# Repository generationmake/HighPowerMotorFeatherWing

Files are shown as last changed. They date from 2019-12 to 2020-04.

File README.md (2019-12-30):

# HighPowerMotorFeatherWing
HighPowerMotorFeatherWing with Infineon IFX007T drivers for two DC motors, up to 40V and 55A, compatible to Adafruit Feather

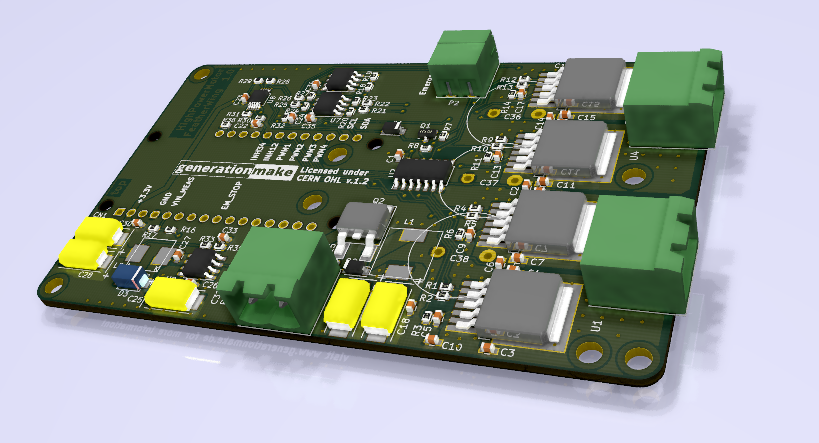
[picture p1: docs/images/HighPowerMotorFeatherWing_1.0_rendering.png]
HighPowerMotorFeatherWing rendering


## PCB

### Top

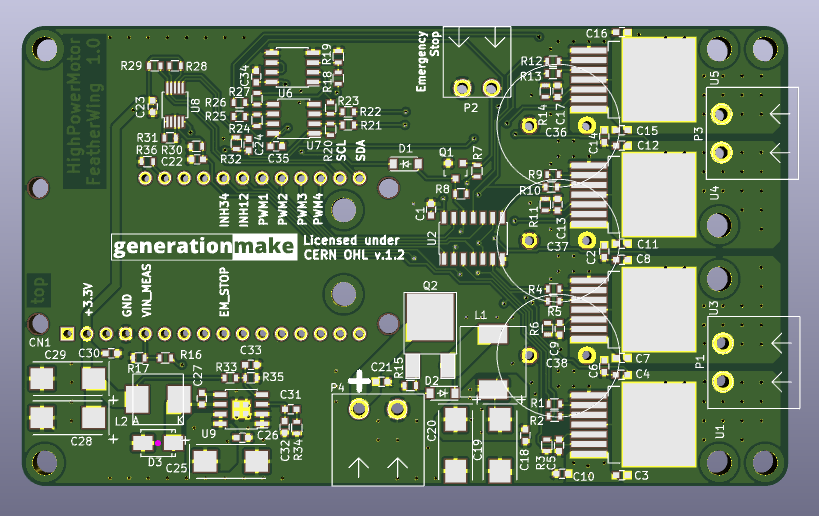
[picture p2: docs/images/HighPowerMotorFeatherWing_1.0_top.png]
HighPowerMotorFeatherWing PCB top


### Bottom

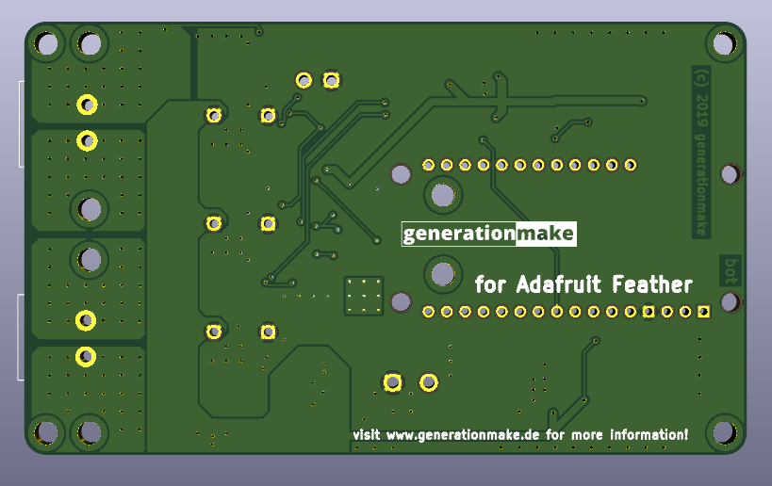
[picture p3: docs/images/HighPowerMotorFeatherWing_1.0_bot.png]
HighPowerMotorFeatherWing PCB bot


## License

This hardware is licensed under the CERN OHL v. 1.2

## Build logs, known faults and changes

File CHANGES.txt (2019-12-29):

HighPowerMotorFeatherWing - Motor driver feather wing for Adafruit Feather
see full project documentation at https://github.com/generationmake/HighPowerMotorFeatherWing

changes

version 1.0 - 2019-12-29
* initial release

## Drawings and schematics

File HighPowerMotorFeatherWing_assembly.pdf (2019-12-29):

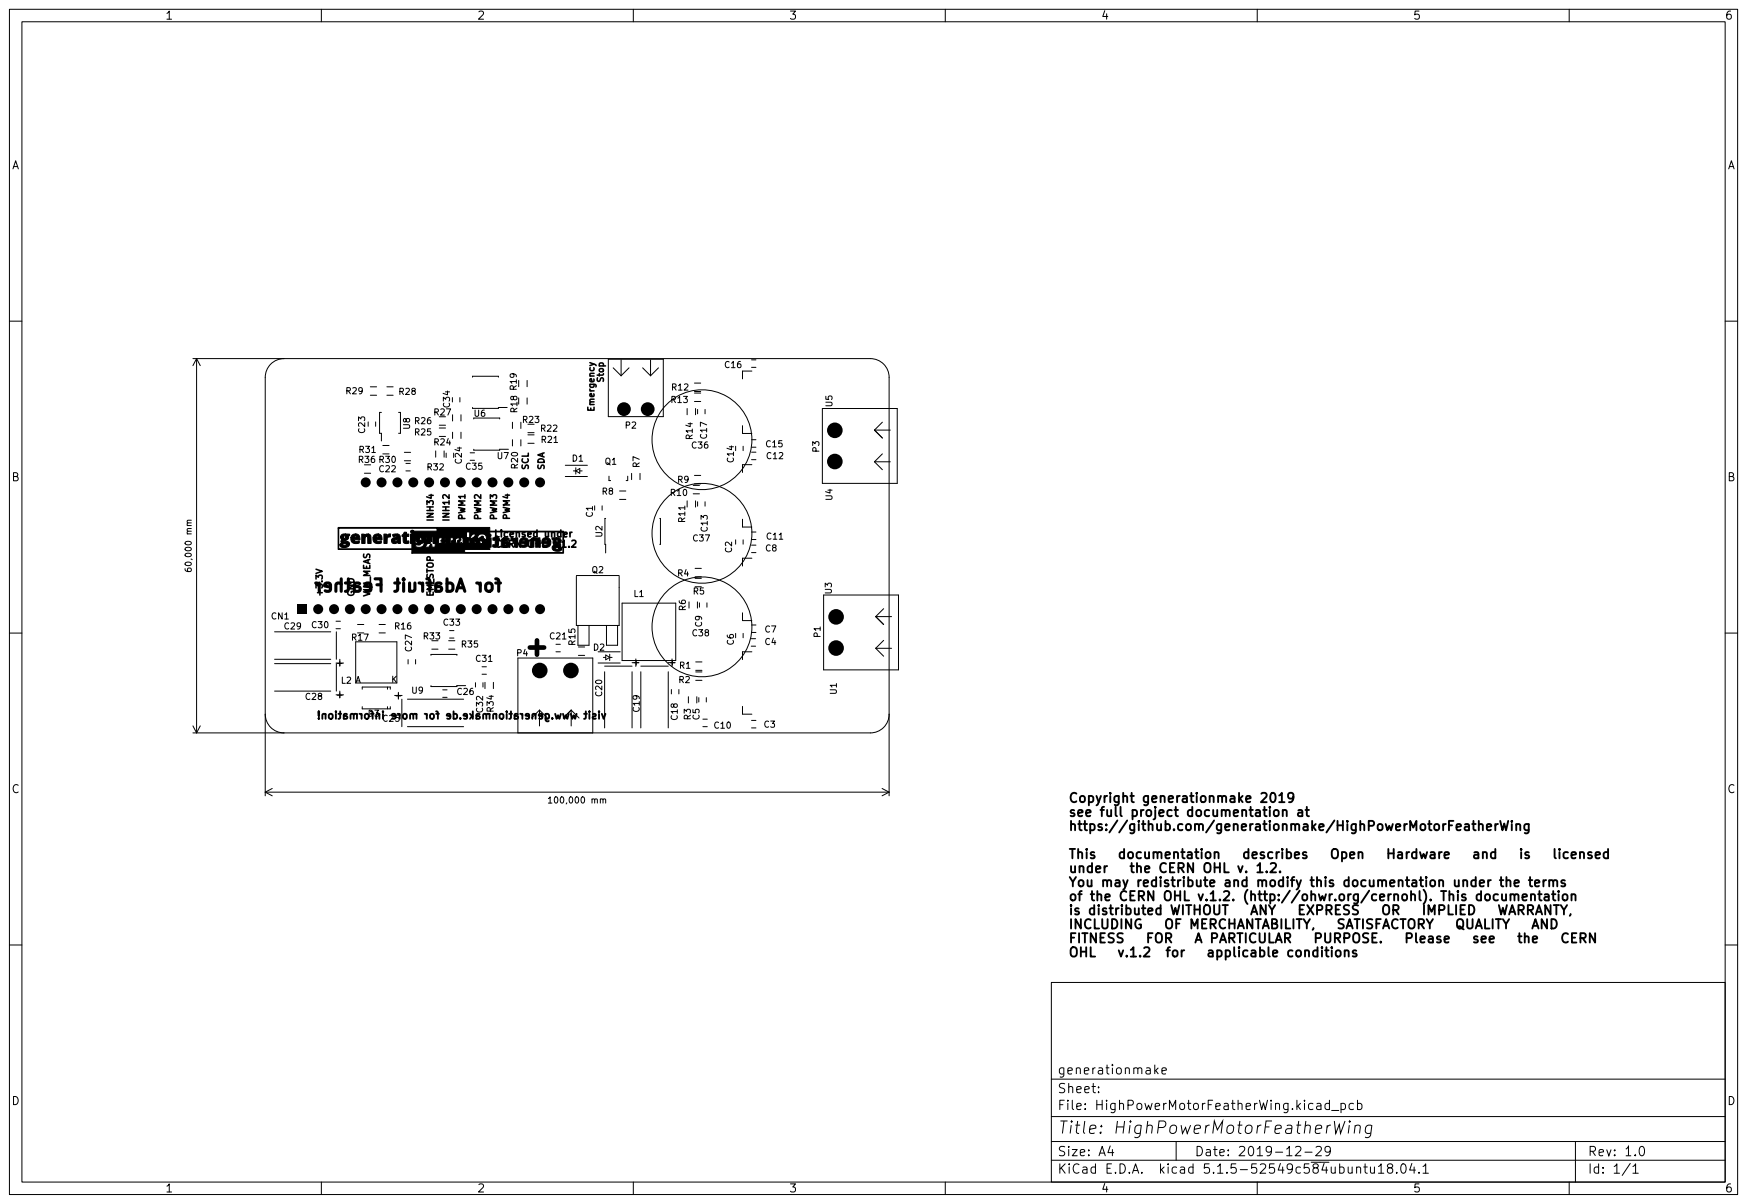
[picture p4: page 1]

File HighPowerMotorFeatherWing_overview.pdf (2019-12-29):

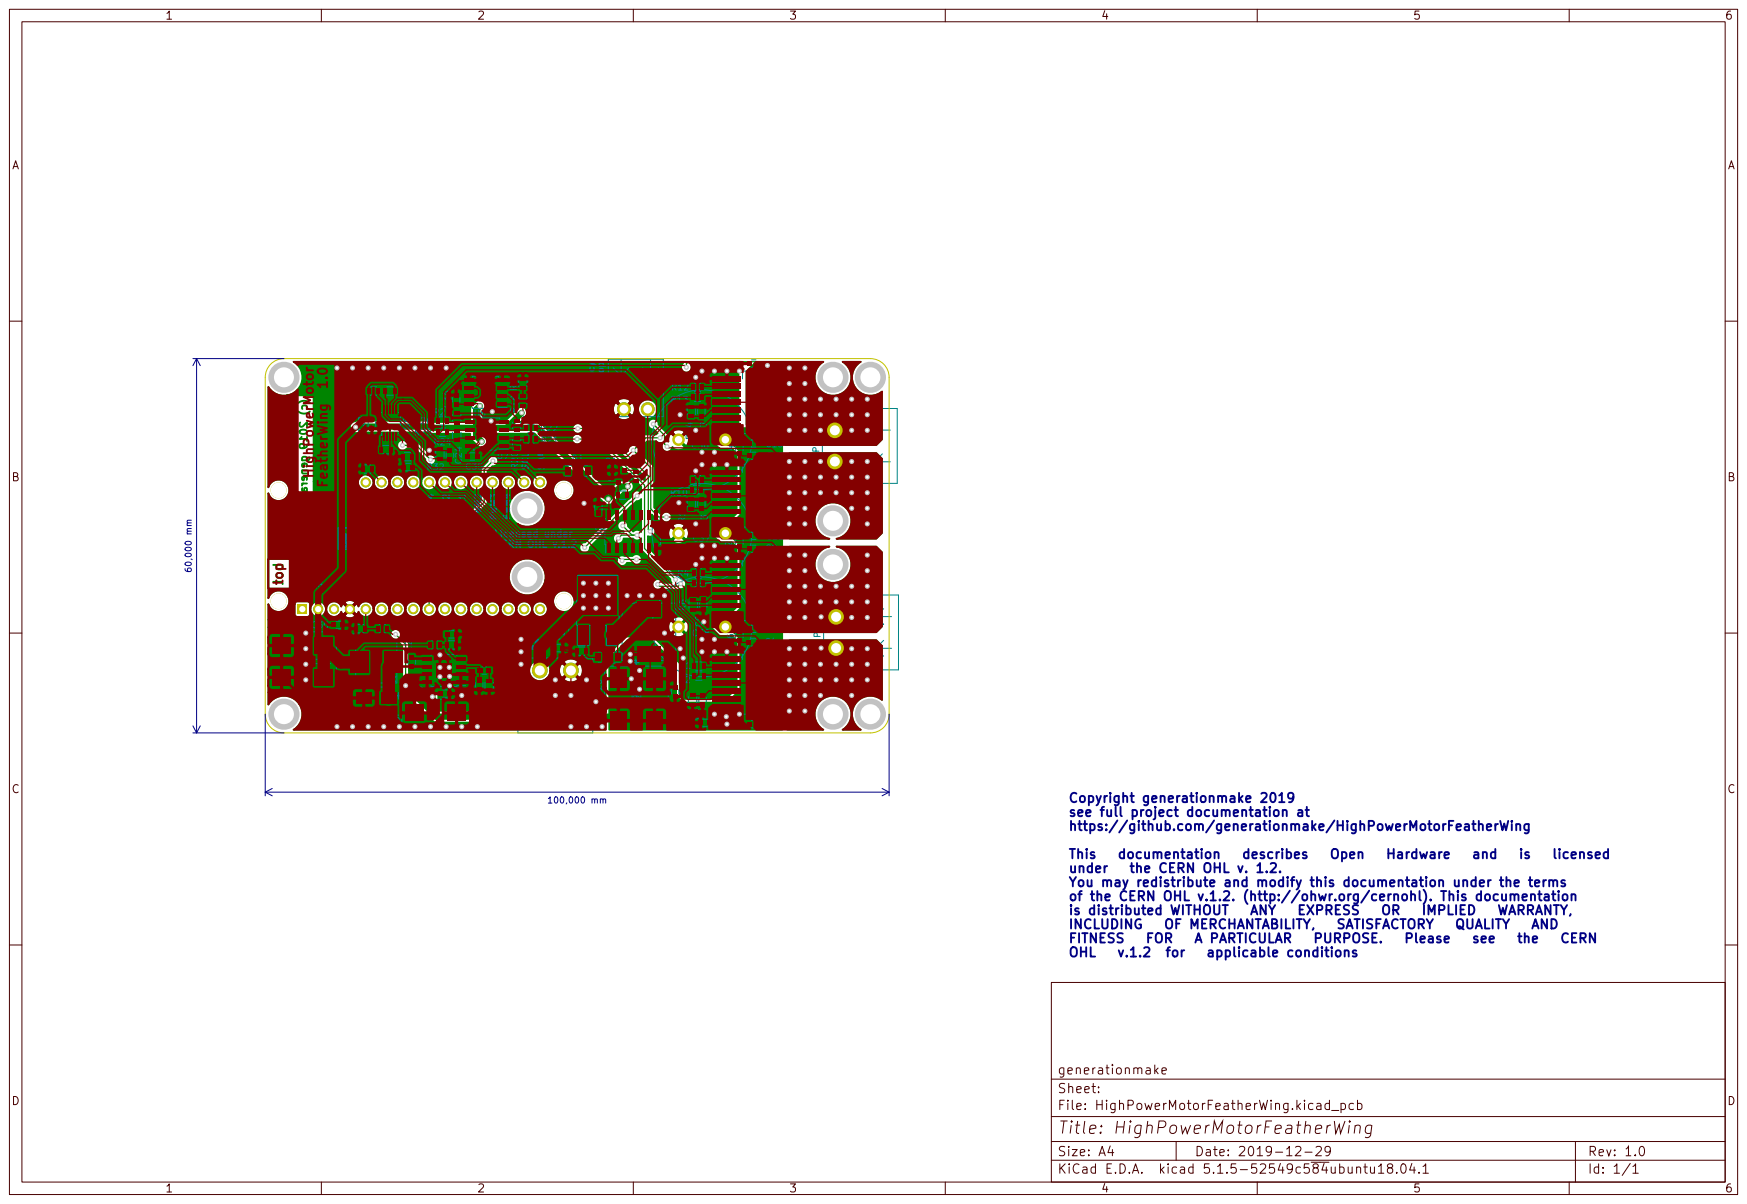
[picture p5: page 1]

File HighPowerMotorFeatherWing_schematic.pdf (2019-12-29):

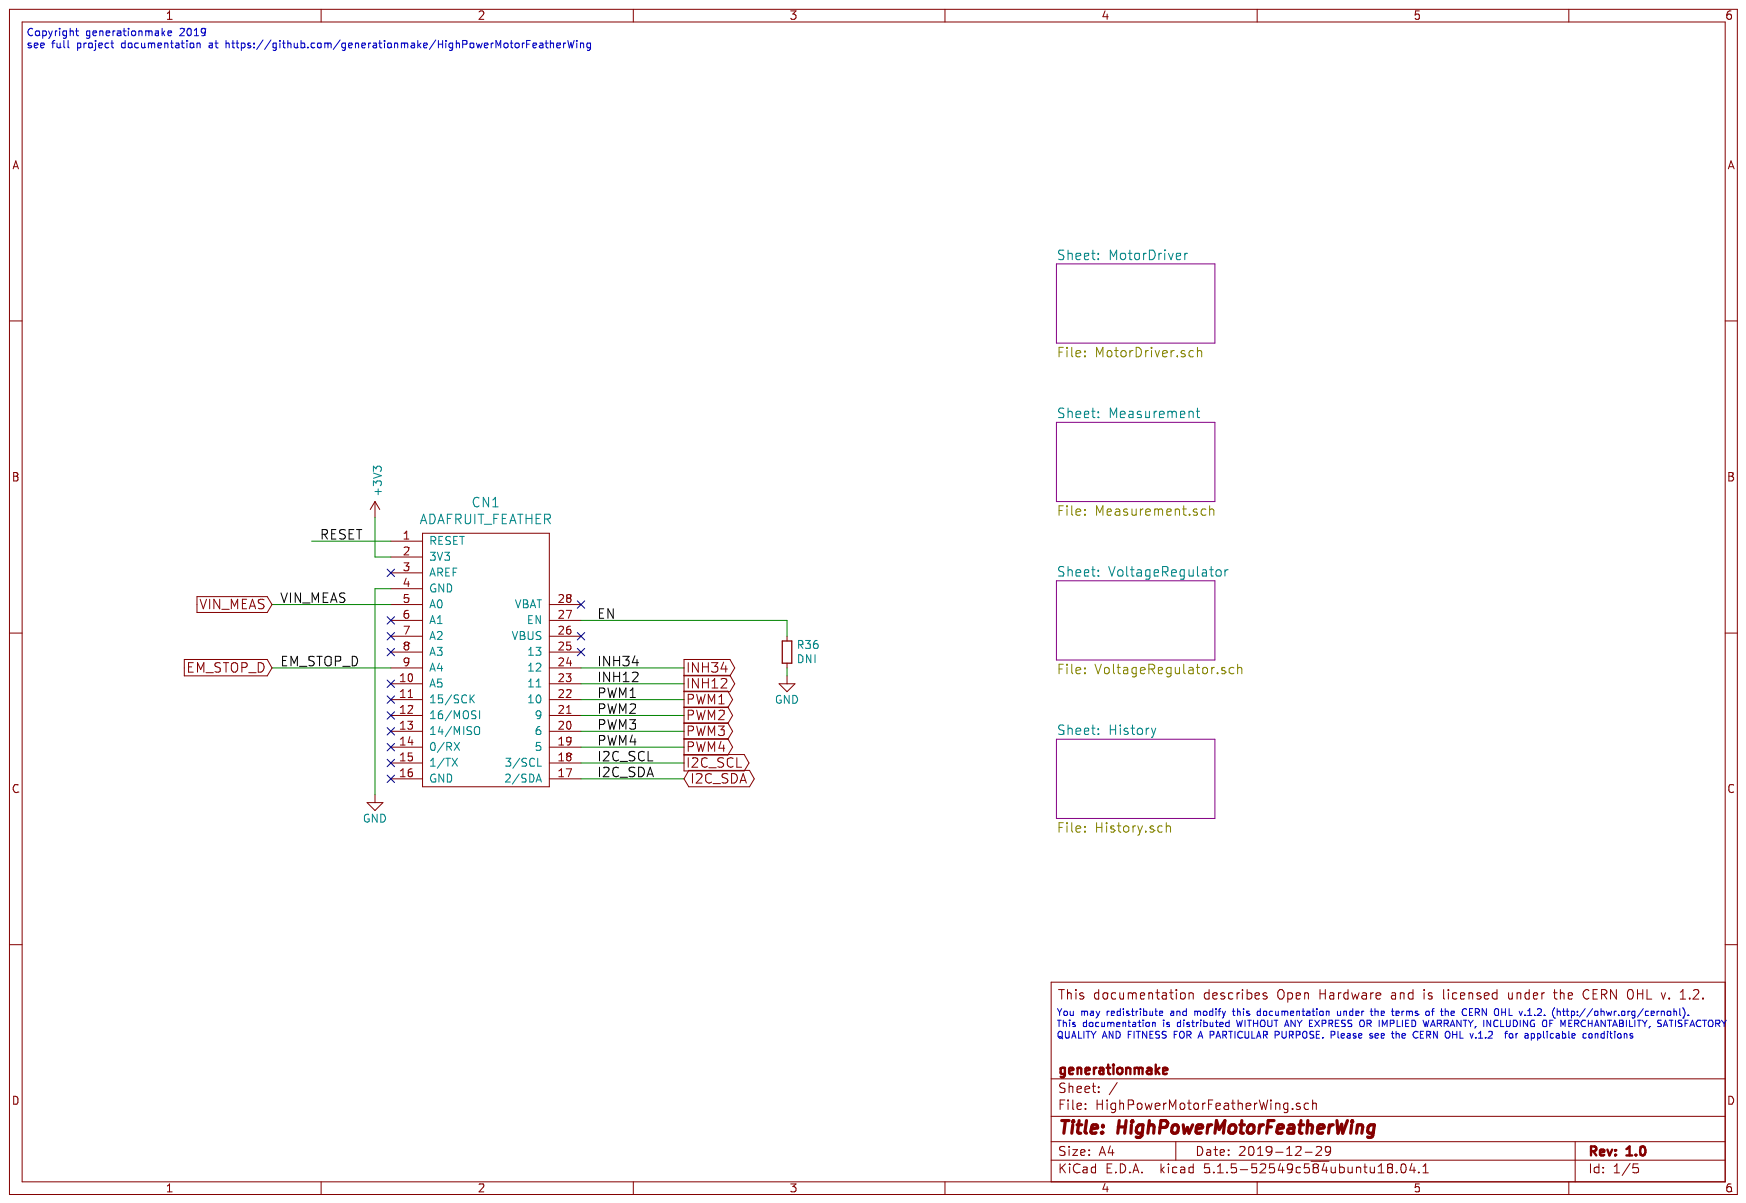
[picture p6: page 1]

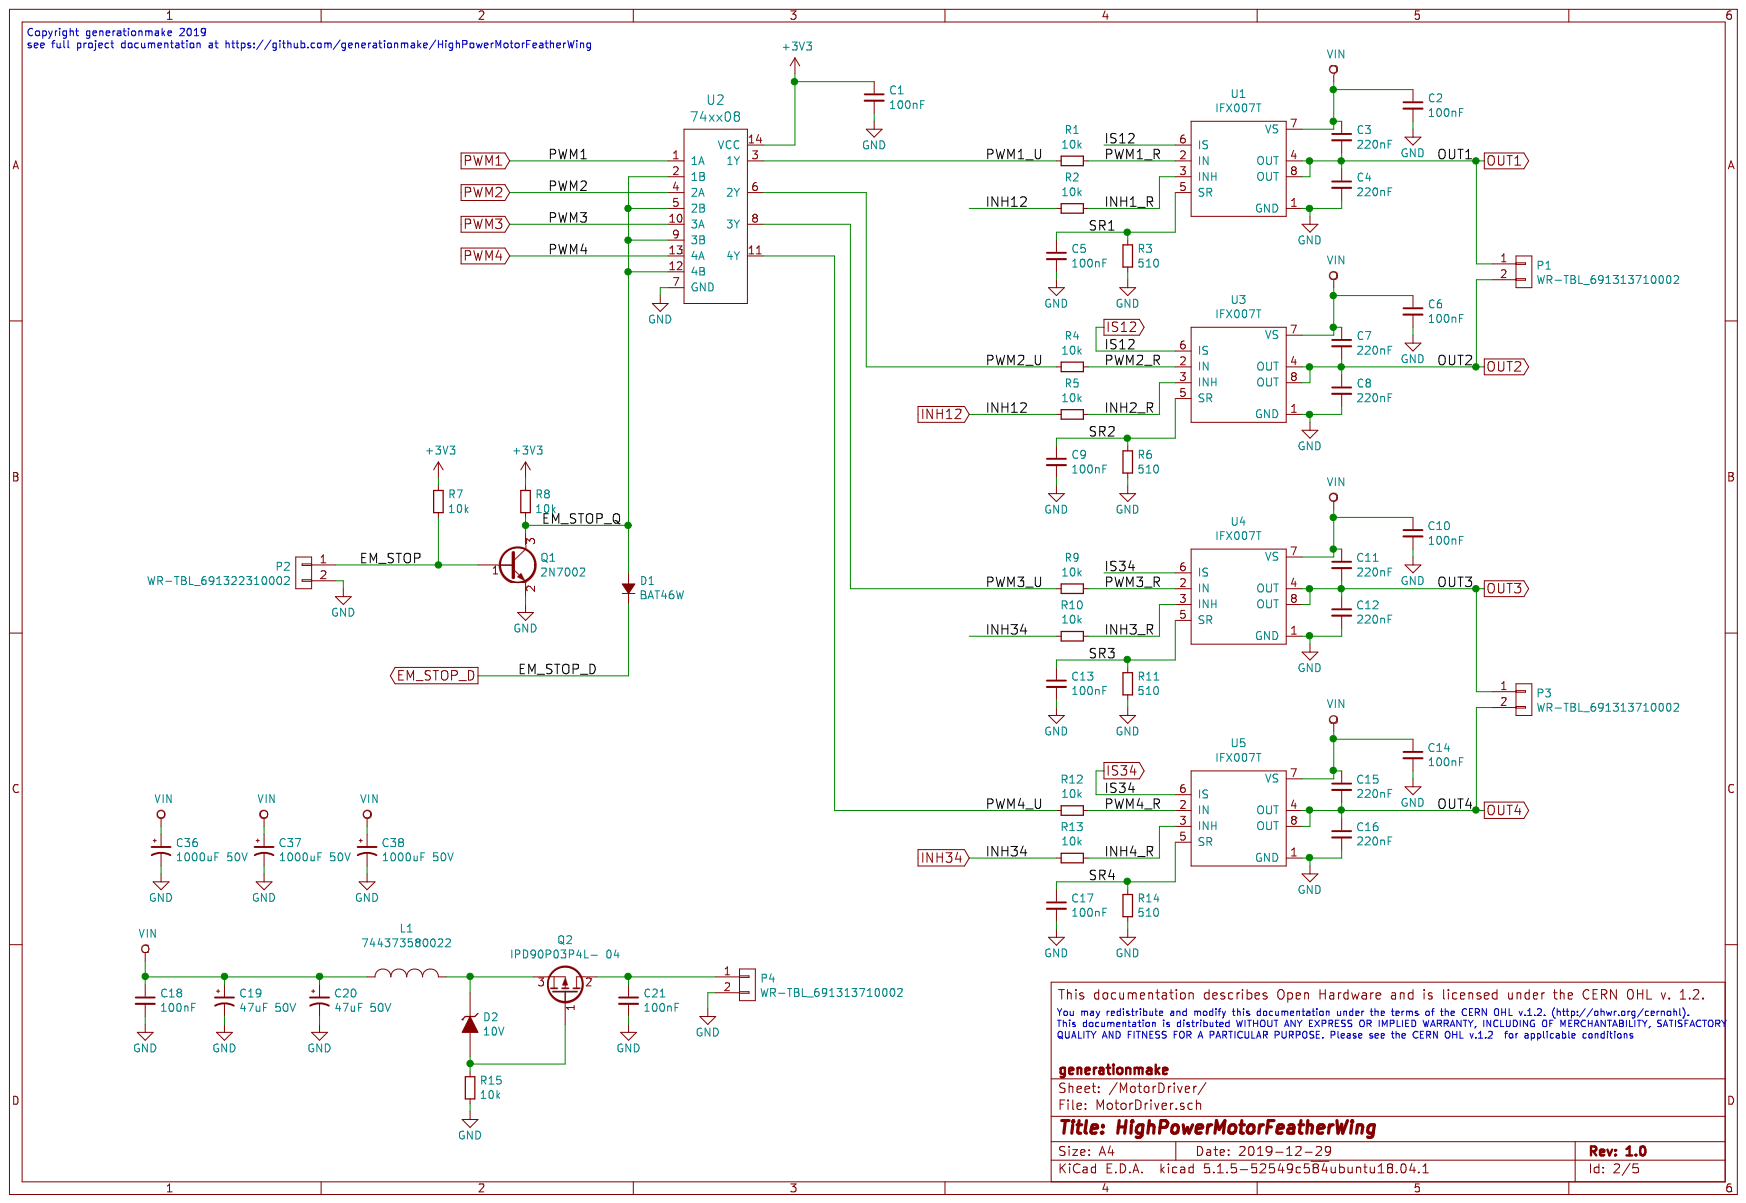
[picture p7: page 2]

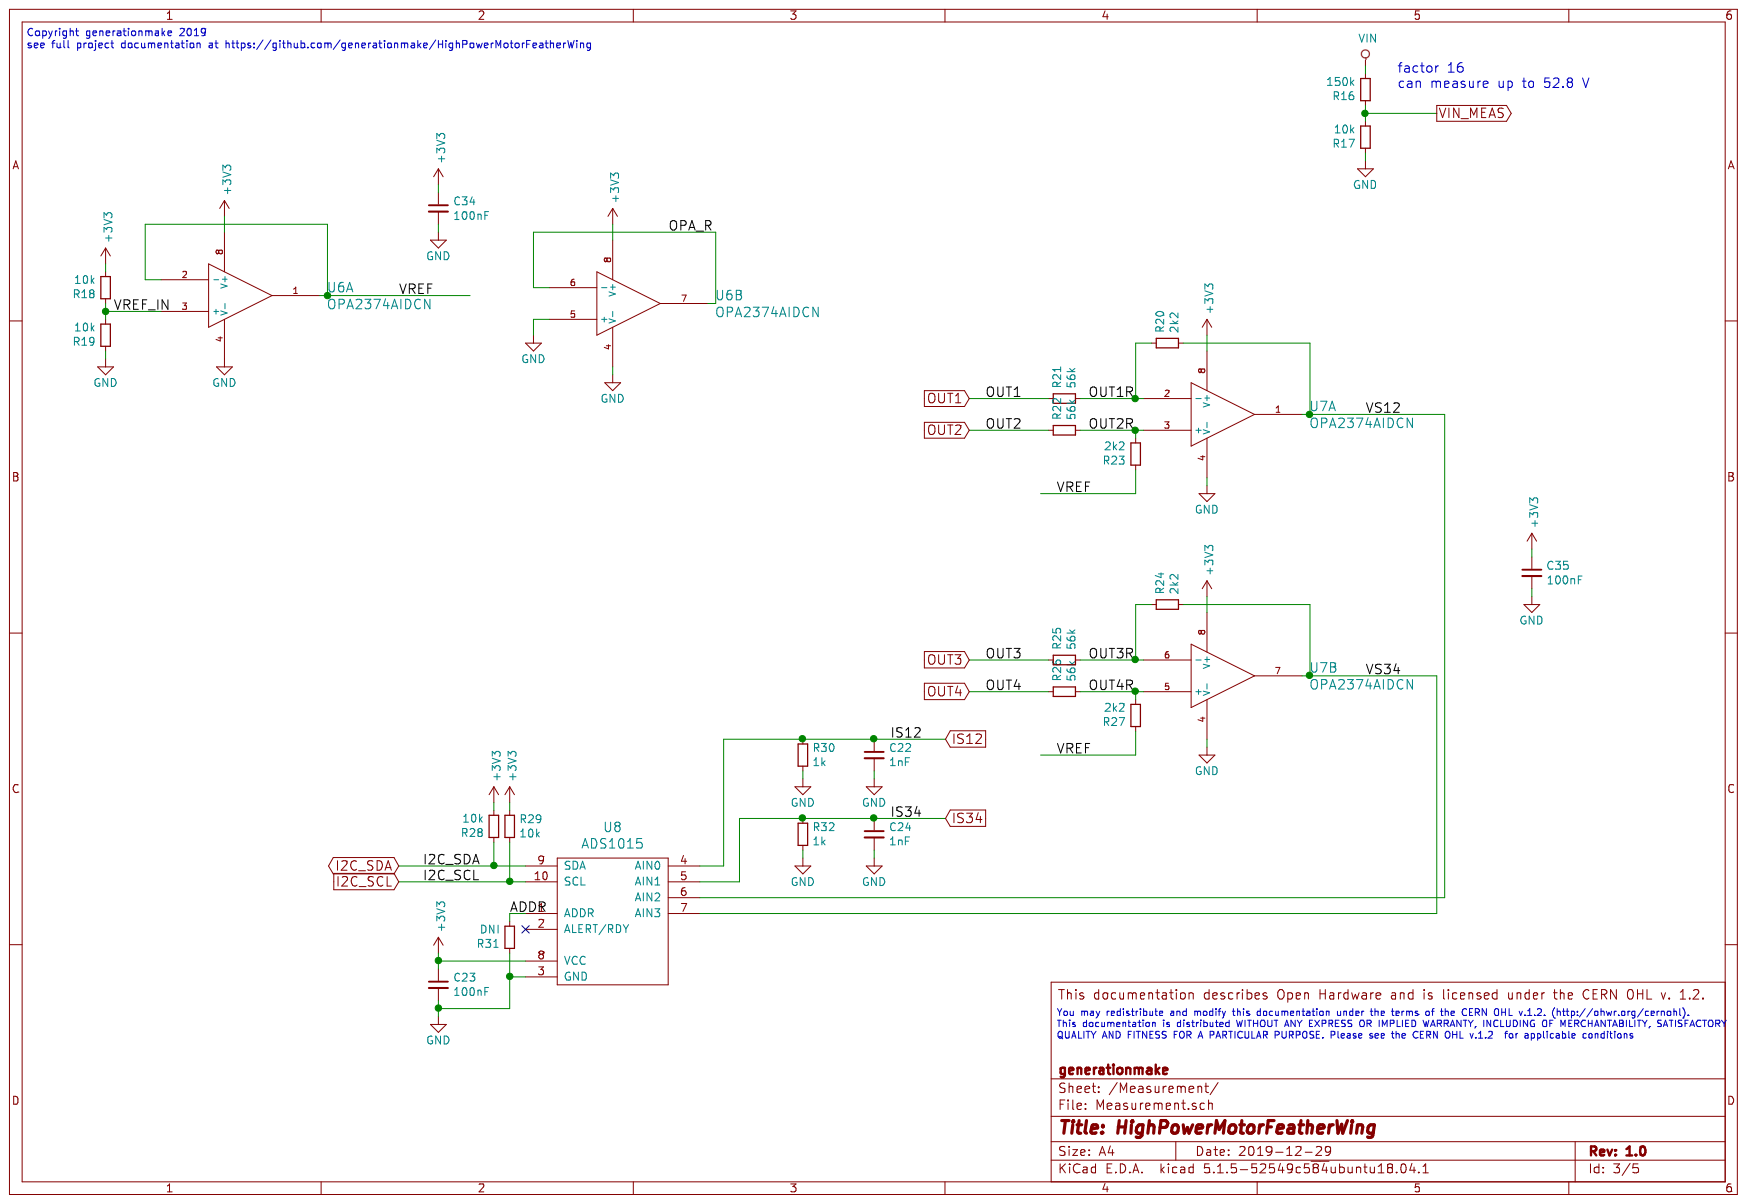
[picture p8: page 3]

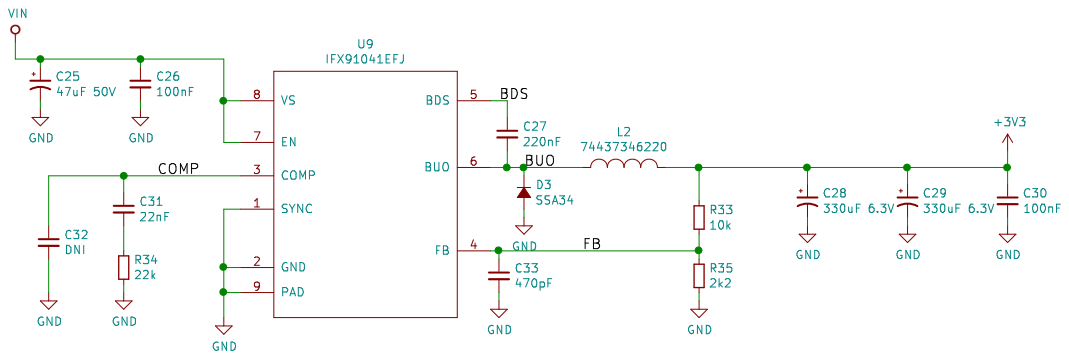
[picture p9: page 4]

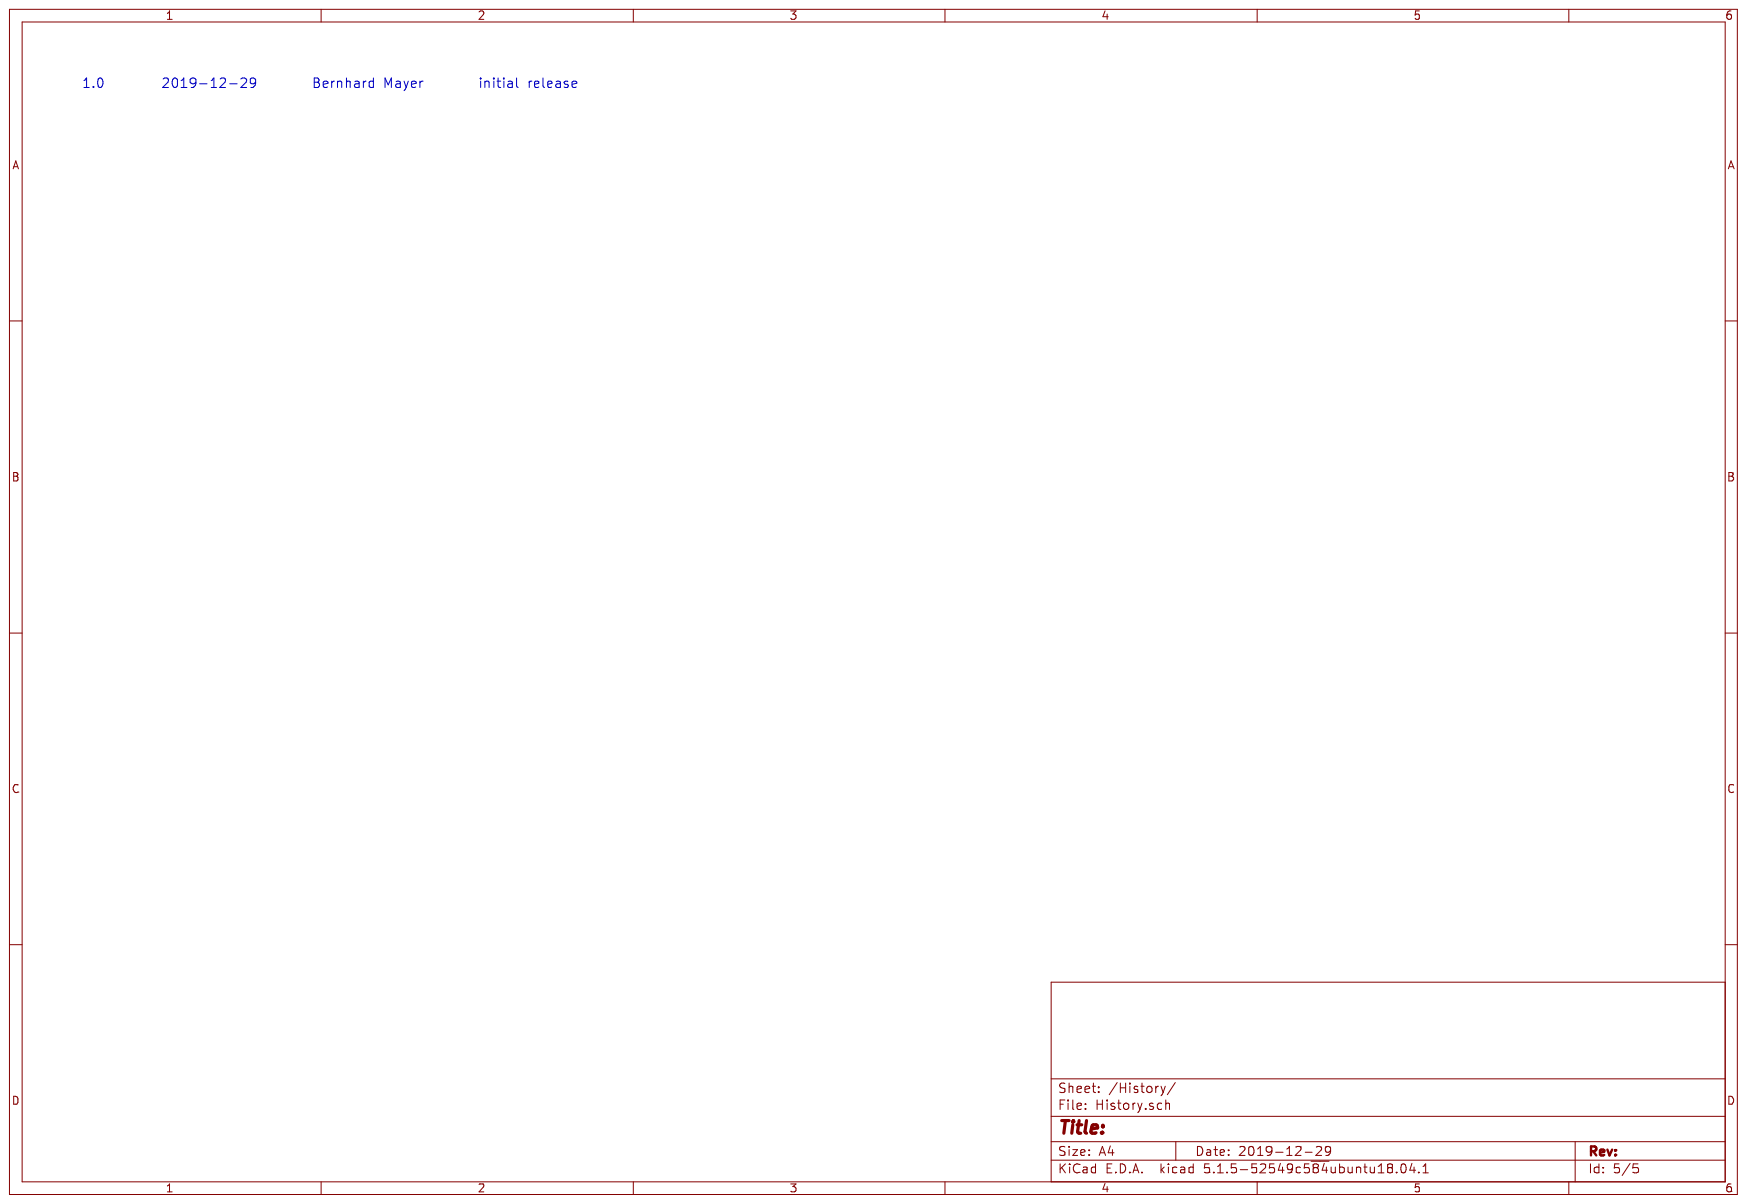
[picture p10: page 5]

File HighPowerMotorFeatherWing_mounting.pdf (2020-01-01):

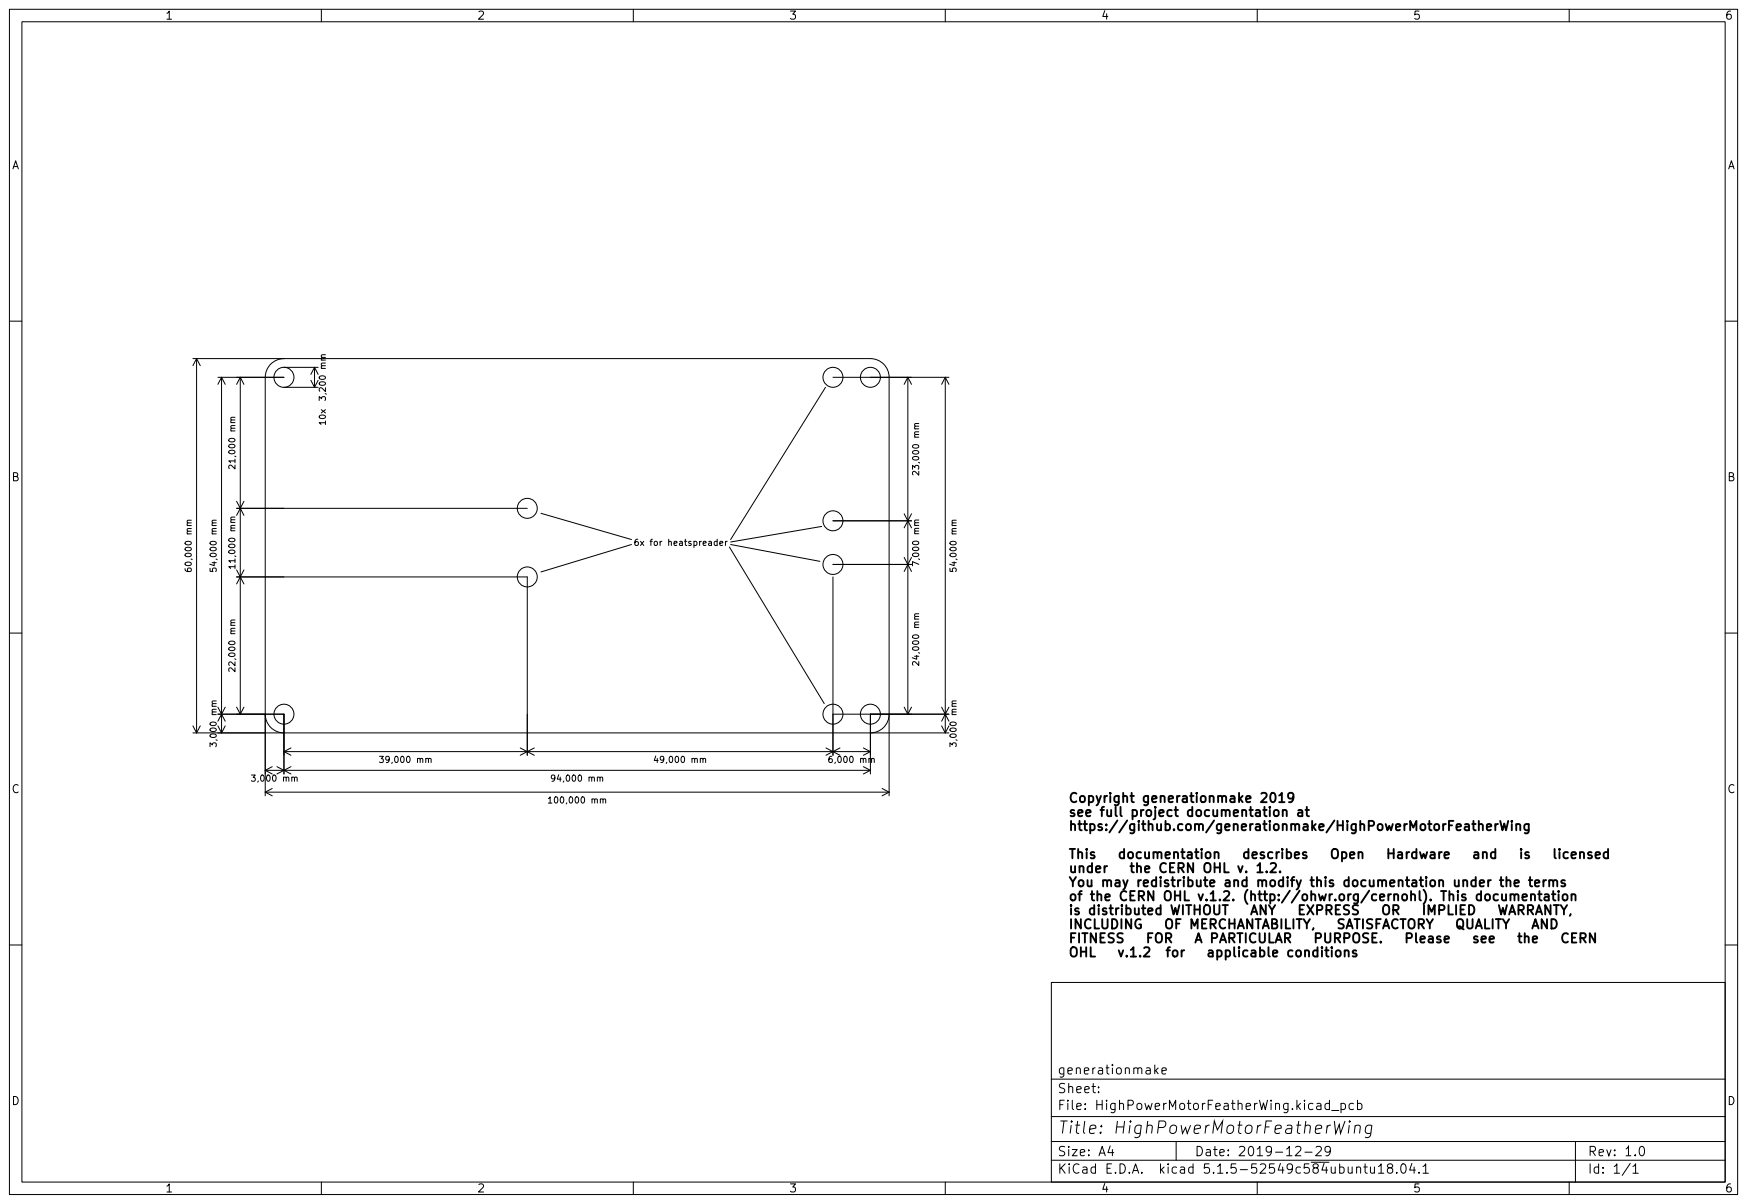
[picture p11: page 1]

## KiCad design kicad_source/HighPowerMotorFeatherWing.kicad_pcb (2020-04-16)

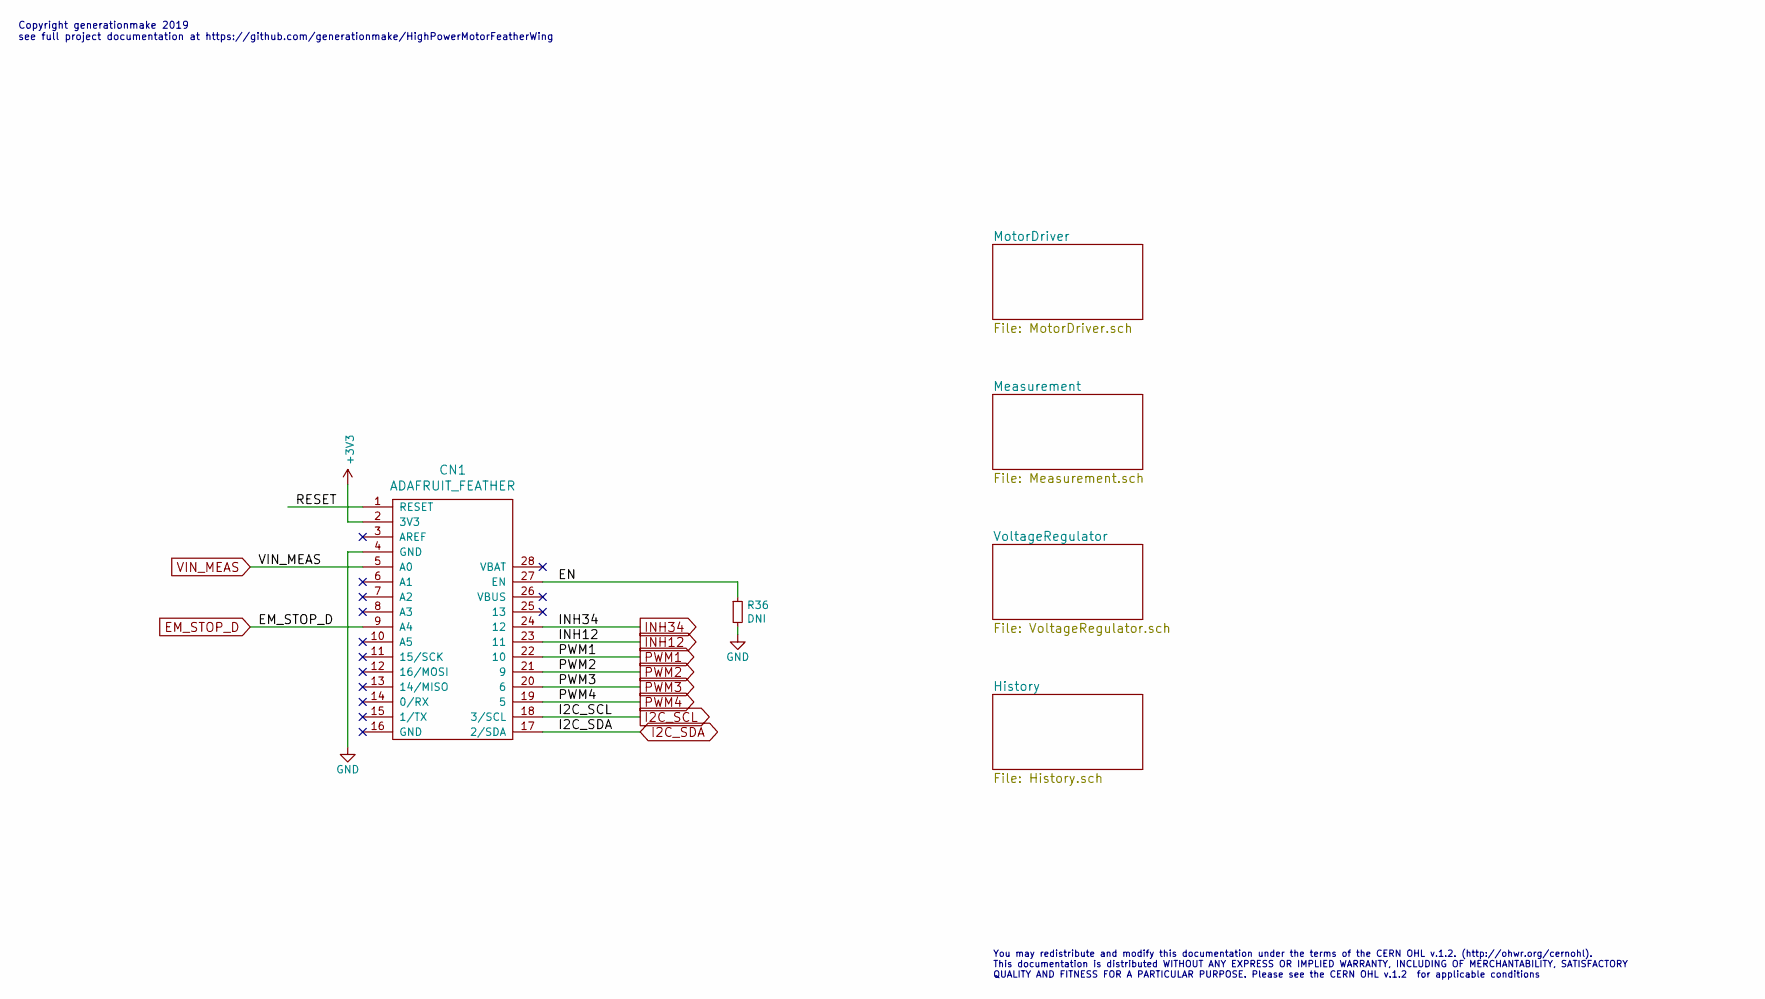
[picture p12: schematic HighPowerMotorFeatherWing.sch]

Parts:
CN1: ADAFRUIT_FEATHER; ADAFRUIT_FEATHER_HOLES
R36: DNI; R_0603

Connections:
+3V3: CN1.2 (3V3); also elsewhere on the board
/EN: CN1.27 (EN), R36.1
EM_STOP_D: CN1.9 (A4); also elsewhere on the board
GND: CN1.4 (GND), R36.2; also elsewhere on the board
I2C_SCL: CN1.18 (3/SCL); also elsewhere on the board
I2C_SDA: CN1.17 (2/SDA); also elsewhere on the board
INH12: CN1.23 (11); also elsewhere on the board
INH34: CN1.24 (12); also elsewhere on the board
PWM1: CN1.22 (10); also elsewhere on the board
PWM2: CN1.21 (9); also elsewhere on the board
PWM3: CN1.20 (6); also elsewhere on the board
PWM4: CN1.19 (5); also elsewhere on the board
VIN_MEAS: CN1.5 (A0); also elsewhere on the board

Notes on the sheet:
Copyright generationmake 2019 see full project documentation at https://github.com/generationmake/HighPowerMotorFeatherWing
You may redistribute and modify this documentation under the terms of the CERN OHL v.1.2. (http://ohwr.org/cernohl). This documentation is distributed WITHOUT ANY EXPRESS OR IMPLIED WARRANTY, INCLUDING OF MERCHANTABILITY, SATISFACTORY QUALITY AND FITNESS FOR A PARTICULAR PURPOSE. Please see the CER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

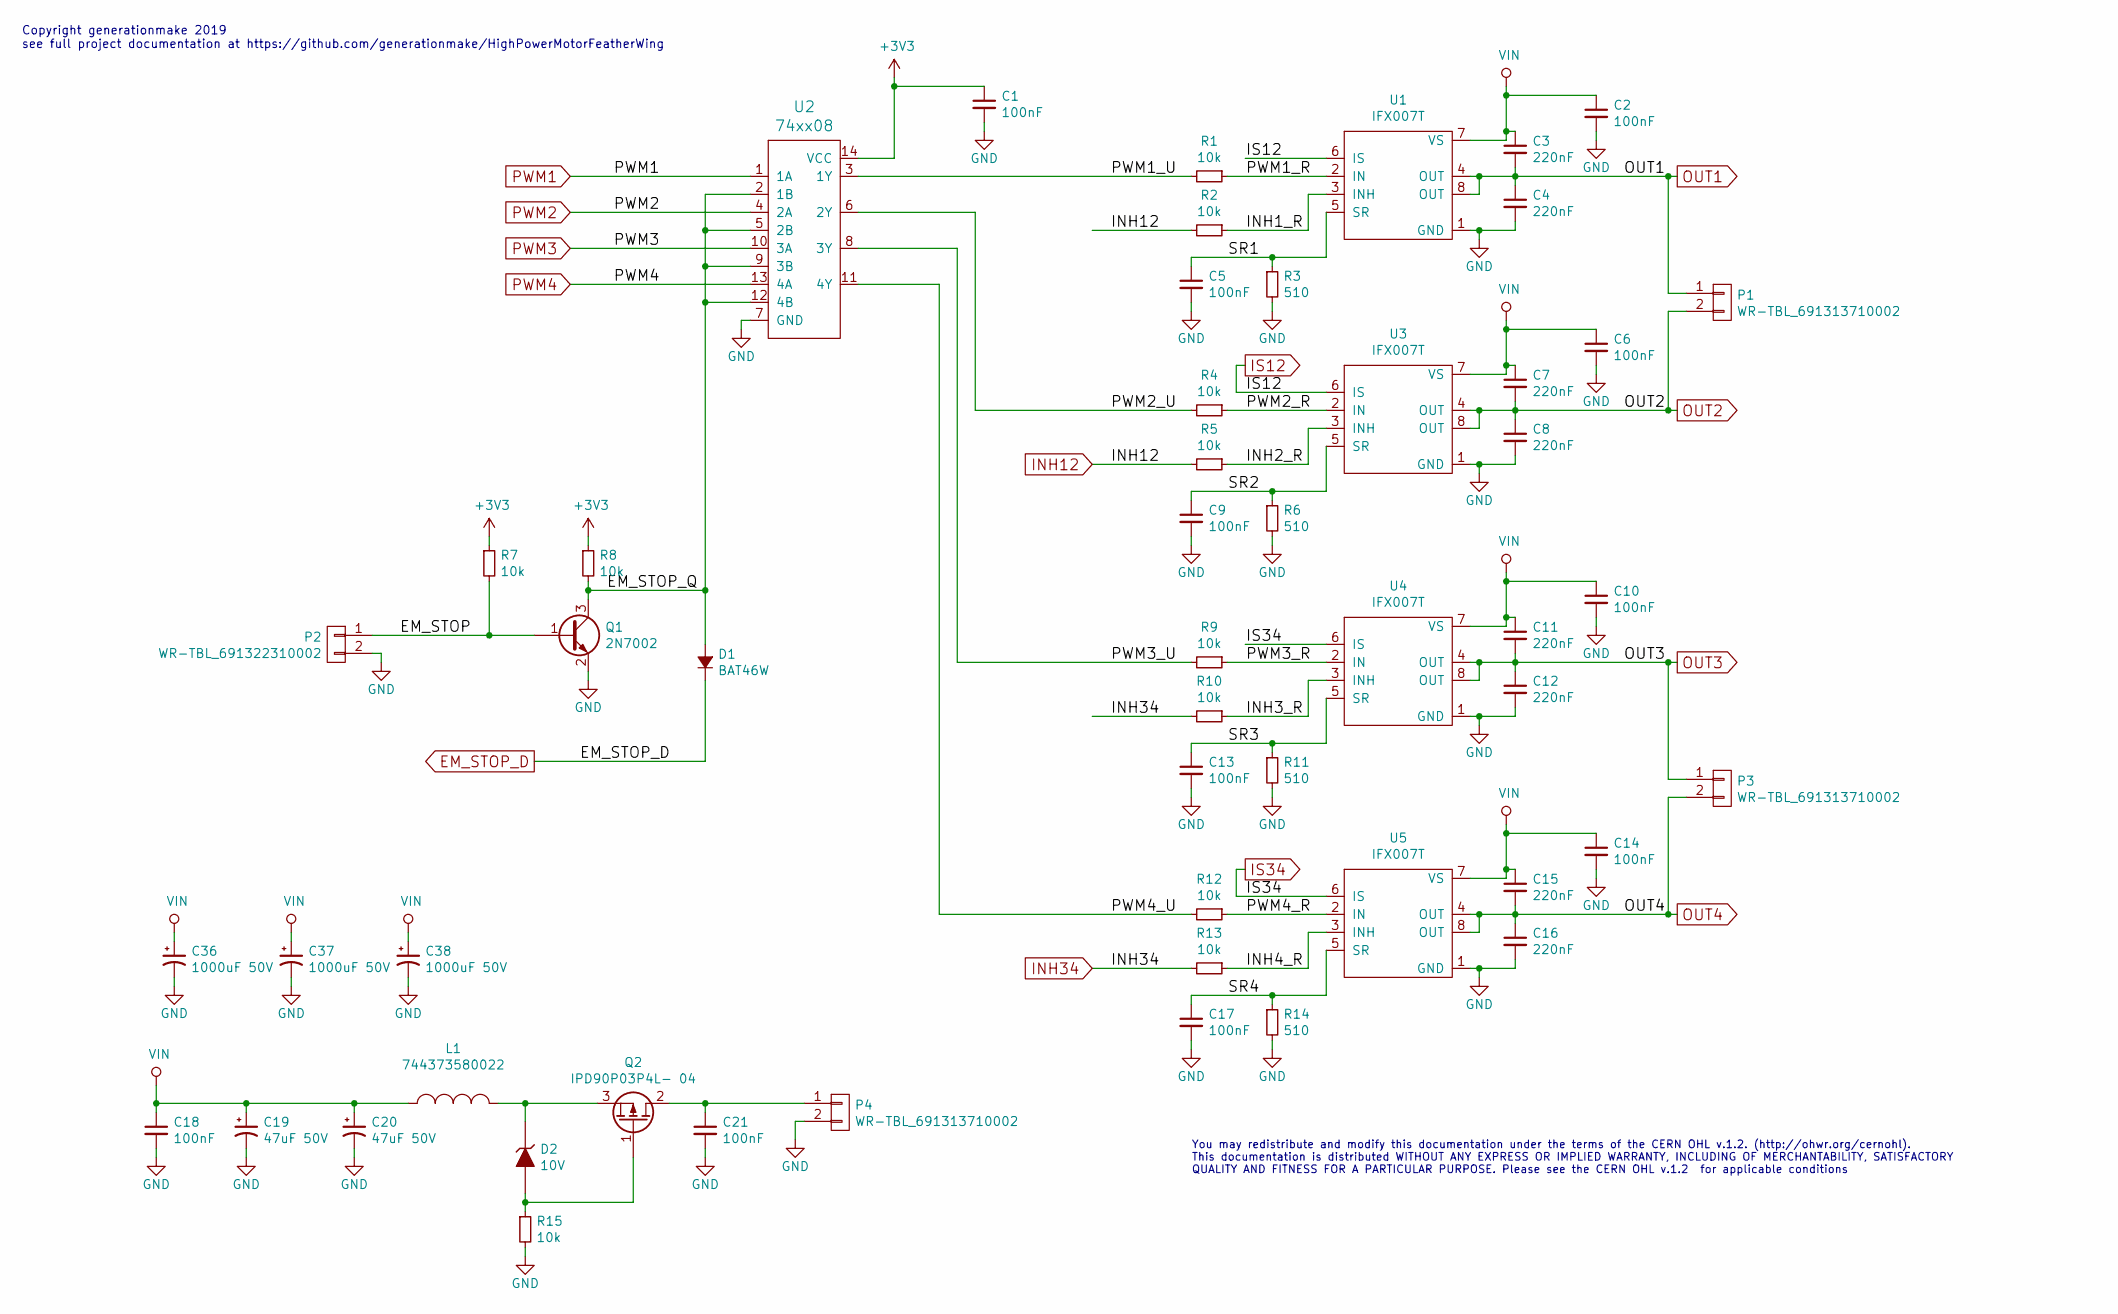
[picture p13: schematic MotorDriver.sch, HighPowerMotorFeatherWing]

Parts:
C1, C2, C5, C6, C9, C10, C13, C14, C17, C18, C21: 100nF; C_0603
C3, C4, C7, C8, C11, C12, C15, C16: 220nF; C_0603
C19, C20: 47uF 50V; TantalC_SizeD_EIA-7343_Wave
C36, C37, C38: 1000uF 50V; C_elec_THT_16x25_RM7.5
D1: BAT46W; SOD-123
D2: 10V; SOD-123
L1: 744373580022; WE-LHMI80xx
P1, P3, P4: WR-TBL_691313710002
P2: WR-TBL_691322310002
Q1: 2N7002; SOT-23
Q2: IPD90P03P4L- 04; TO-252-2Lead
R1, R2, R4, R5, R7, R8, R9, R10, R12, R13, R15: 10k; R_0603
R3, R6, R11, R14: 510; R_0603
U1, U3, U4, U5: IFX007T; TO-263-7Lead
U2: 74xx08; SOIC-14_3.9x8.7mm_Pitch1.27mm

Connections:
+3V3: C1.1, R7.1, R8.1, U2.14 (VCC); also elsewhere on the board
/MotorDriver/EM_STOP: P2.1, Q1.1 (B), R7.2
/MotorDriver/EM_STOP_Q: D1.2 (A), Q1.3 (C), R8.2, U2.2 (1B), U2.5 (2B), U2.9 (3B), U2.12 (4B)
/MotorDriver/INH1_R: R2.1, U1.3 (INH)
/MotorDriver/INH2_R: R5.1, U3.3 (INH)
/MotorDriver/INH3_R: R10.1, U4.3 (INH)
/MotorDriver/INH4_R: R13.1, U5.3 (INH)
/MotorDriver/PWM1_R: R1.1, U1.2 (IN)
/MotorDriver/PWM1_U: R1.2, U2.3 (1Y)
/MotorDriver/PWM2_R: R4.1, U3.2 (IN)
/MotorDriver/PWM2_U: R4.2, U2.6 (2Y)
/MotorDriver/PWM3_R: R9.1, U4.2 (IN)
/MotorDriver/PWM3_U: R9.2, U2.8 (3Y)
/MotorDriver/PWM4_R: R12.1, U5.2 (IN)
/MotorDriver/PWM4_U: R12.2, U2.11 (4Y)
/MotorDriver/SR1: C5.1, R3.1, U1.5 (SR)
/MotorDriver/SR2: C9.1, R6.1, U3.5 (SR)
/MotorDriver/SR3: C13.1, R11.1, U4.5 (SR)
/MotorDriver/SR4: C17.1, R14.1, U5.5 (SR)
EM_STOP_D: D1.1 (K); also elsewhere on the board
GND: C1.2, C2.2, C4.2, C5.2, C6.2, C8.2, C9.2, C10.2, C12.2, C13.2, C14.2, C16.2, C17.2, C18.2, C19.2, C20.2, C21.2, C36.2, C37.2, C38.2, P2.2, P4.2, Q1.2 (E), R3.2, R6.2, R11.2, R14.2, R15.2, U1.1 (GND), U2.7 (GND), U3.1 (GND), U4.1 (GND), U5.1 (GND); also elsewhere on the board
INH12: R2.2, R5.2; also elsewhere on the board
INH34: R10.2, R13.2; also elsewhere on the board
IS12: U1.6 (IS), U3.6 (IS); also elsewhere on the board
IS34: U4.6 (IS), U5.6 (IS); also elsewhere on the board
unnamed: C21.1, P4.1, Q2.2 (D)
unnamed: D2.1 (K), L1.2, Q2.3 (S)
unnamed: D2.2 (A), Q2.1 (G), R15.1
OUT1: C3.2, C4.1, P1.1, U1.4 (OUT), U1.8 (OUT); also elsewhere on the board
OUT2: C7.2, C8.1, P1.2, U3.4 (OUT), U3.8 (OUT); also elsewhere on the board
OUT3: C11.2, C12.1, P3.1, U4.4 (OUT), U4.8 (OUT); also elsewhere on the board
OUT4: C15.2, C16.1, P3.2, U5.4 (OUT), U5.8 (OUT); also elsewhere on the board
PWM1: U2.1 (1A); also elsewhere on the board
PWM2: U2.4 (2A); also elsewhere on the board
PWM3: U2.10 (3A); also elsewhere on the board
PWM4: U2.13 (4A); also elsewhere on the board
VIN: C2.1, C3.1, C6.1, C7.1, C10.1, C11.1, C14.1, C15.1, C18.1, C19.1, C20.1, C36.1, C37.1, C38.1, L1.1, U1.7 (VS), U3.7 (VS), U4.7 (VS), U5.7 (VS); also elsewhere on the board

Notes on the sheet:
Copyright generationmake 2019 see full project documentation at https://github.com/generationmake/HighPowerMotorFeatherWing
You may redistribute and modify this documentation under the terms of the CERN OHL v.1.2. (http://ohwr.org/cernohl). This documentation is distributed WITHOUT ANY EXPRESS OR IMPLIED WARRANTY, INCLUDING OF MERCHANTABILITY, SATISFACTORY QUALITY AND FITNESS FOR A PARTICULAR PURPOSE. Please see the CER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

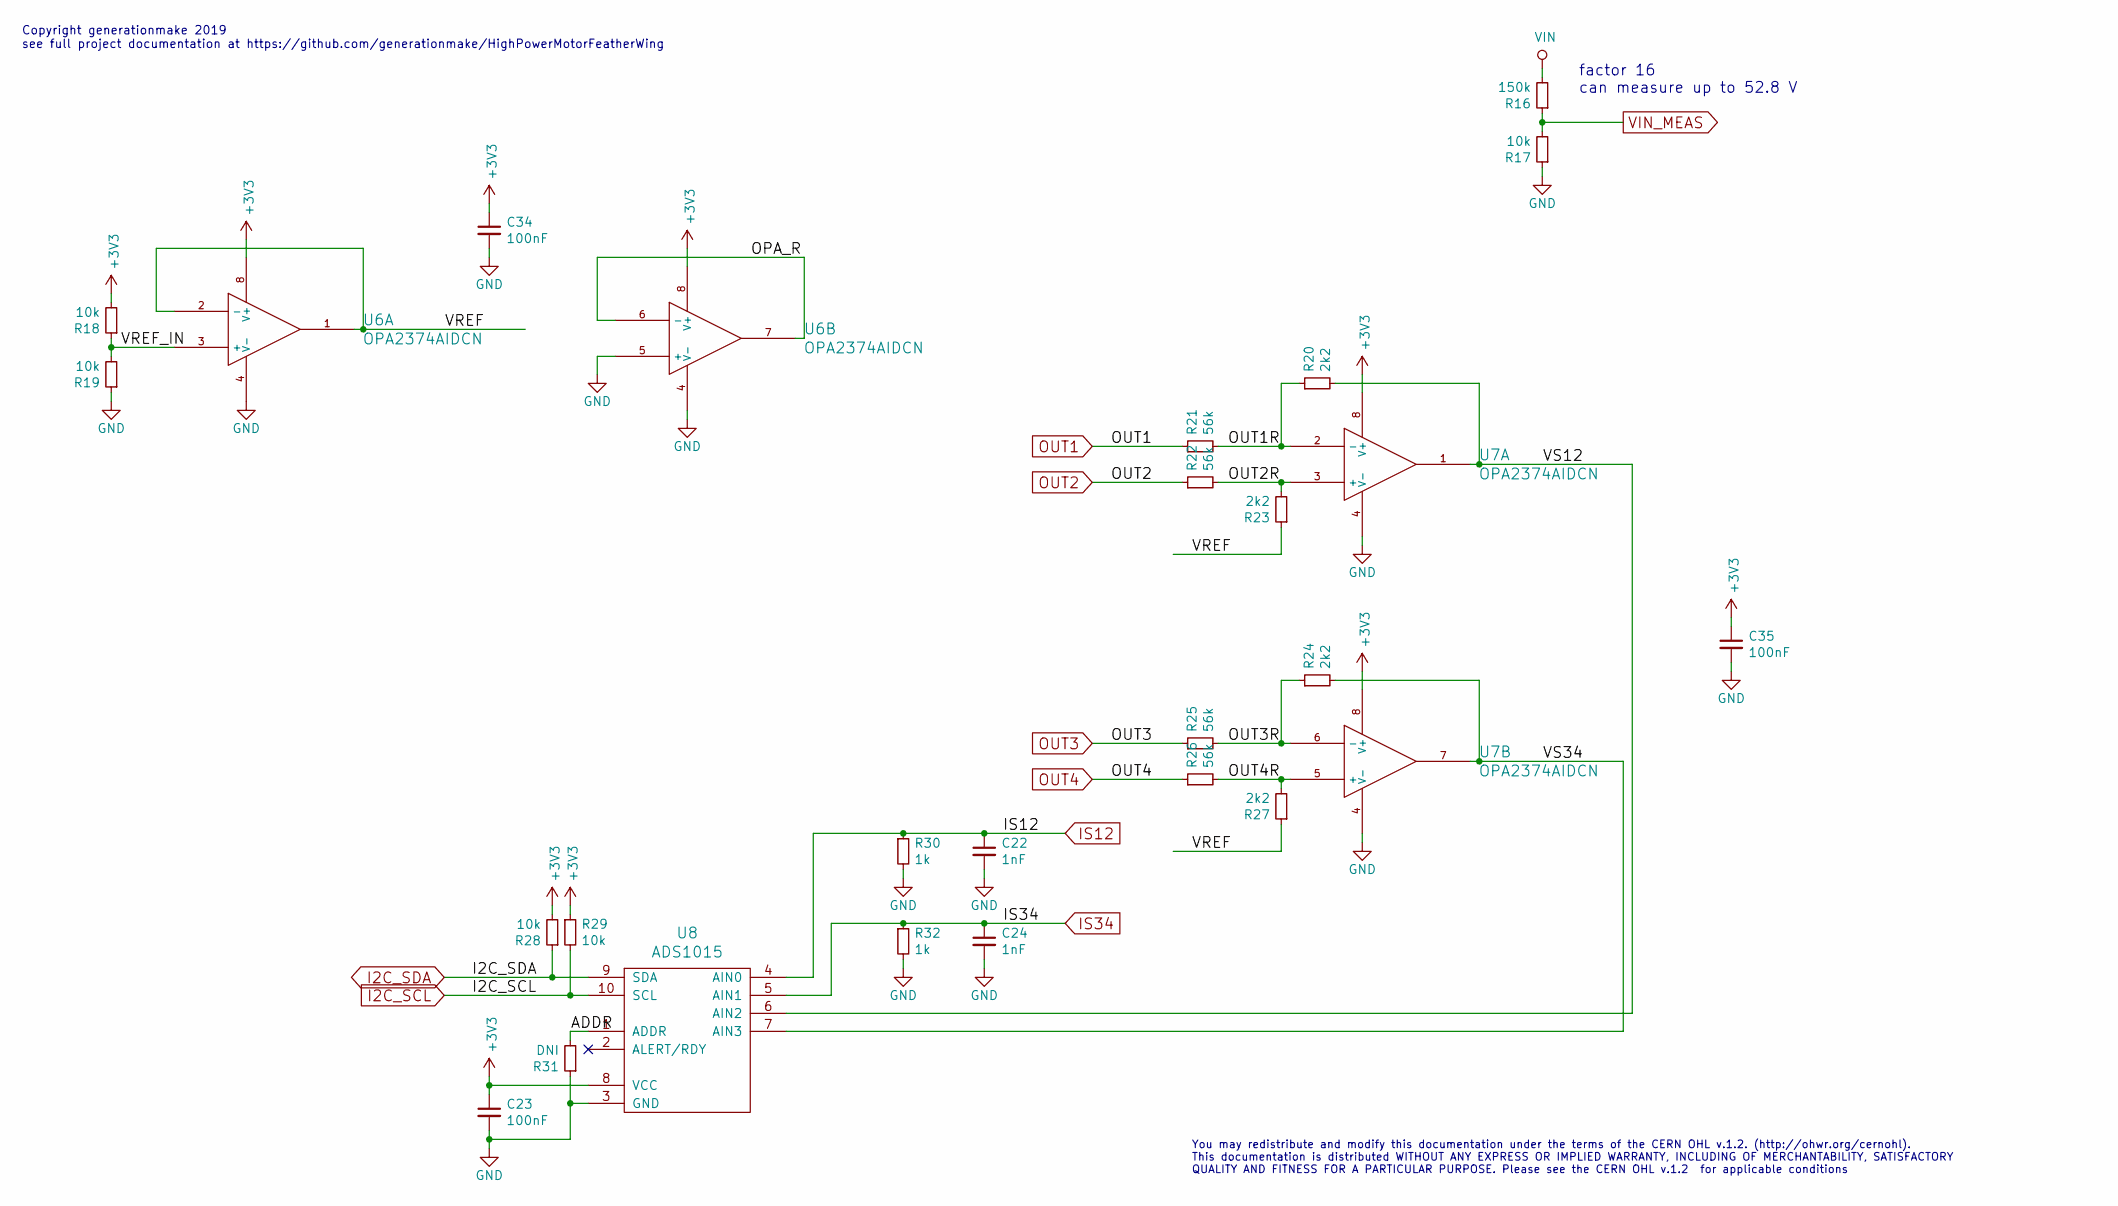
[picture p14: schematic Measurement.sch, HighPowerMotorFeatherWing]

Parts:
C22, C24: 1nF; C_0603
C23, C34, C35: 100nF; C_0603
R16: 150k; R_0603
R17, R18, R19, R28, R29: 10k; R_0603
R20, R23, R24, R27: 2k2; R_0603
R21, R22, R25, R26: 56k; R_0603
R30, R32: 1k; R_0603
R31: DNI; R_0603
U6, U7: OPA2374AIDCN; SOIC-8_3.9x4.9mm_Pitch1.27mm
U8: ADS1015; MSOP-10_3x3mm_Pitch0.5mm

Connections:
+3V3: C23.1, C34.1, C35.1, R18.2, R28.2, R29.1, U6.8 (V+), U7.8 (V+), U8.8 (VCC); also elsewhere on the board
/Measurement/ADDR: R31.2, U8.1 (ADDR)
/Measurement/OPA_R: U6.6 (-), U6.7
/Measurement/OUT1R: R20.1, R21.2, U7.2 (-)
/Measurement/OUT2R: R22.2, R23.2, U7.3 (+)
/Measurement/OUT3R: R24.1, R25.2, U7.6 (-)
/Measurement/OUT4R: R26.2, R27.2, U7.5 (+)
/Measurement/VREF: R23.1, R27.1, U6.1, U6.2 (-)
/Measurement/VREF_IN: R18.1, R19.2, U6.3 (+)
/Measurement/VS12: R20.2, U7.1, U8.6 (AIN2)
/Measurement/VS34: R24.2, U7.7, U8.7 (AIN3)
GND: C22.2, C23.2, C24.2, C34.2, C35.2, R17.1, R19.1, R30.2, R31.1, R32.2, U6.4 (V-), U6.5 (+), U7.4 (V-), U8.3 (GND); also elsewhere on the board
I2C_SCL: R29.2, U8.10 (SCL); also elsewhere on the board
I2C_SDA: R28.1, U8.9 (SDA); also elsewhere on the board
IS12: C22.1, R30.1, U8.4 (AIN0); also elsewhere on the board
IS34: C24.1, R32.1, U8.5 (AIN1); also elsewhere on the board
OUT1: R21.1; also elsewhere on the board
OUT2: R22.1; also elsewhere on the board
OUT3: R25.1; also elsewhere on the board
OUT4: R26.1; also elsewhere on the board
VIN: R16.2; also elsewhere on the board
VIN_MEAS: R16.1, R17.2; also elsewhere on the board

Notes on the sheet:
Copyright generationmake 2019 see full project documentation at https://github.com/generationmake/HighPowerMotorFeatherWing
You may redistribute and modify this documentation under the terms of the CERN OHL v.1.2. (http://ohwr.org/cernohl). This documentation is distributed WITHOUT ANY EXPRESS OR IMPLIED WARRANTY, INCLUDING OF MERCHANTABILITY, SATISFACTORY QUALITY AND FITNESS FOR A PARTICULAR PURPOSE. Please see the CER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
factor 16 can measure up to 52.8 V

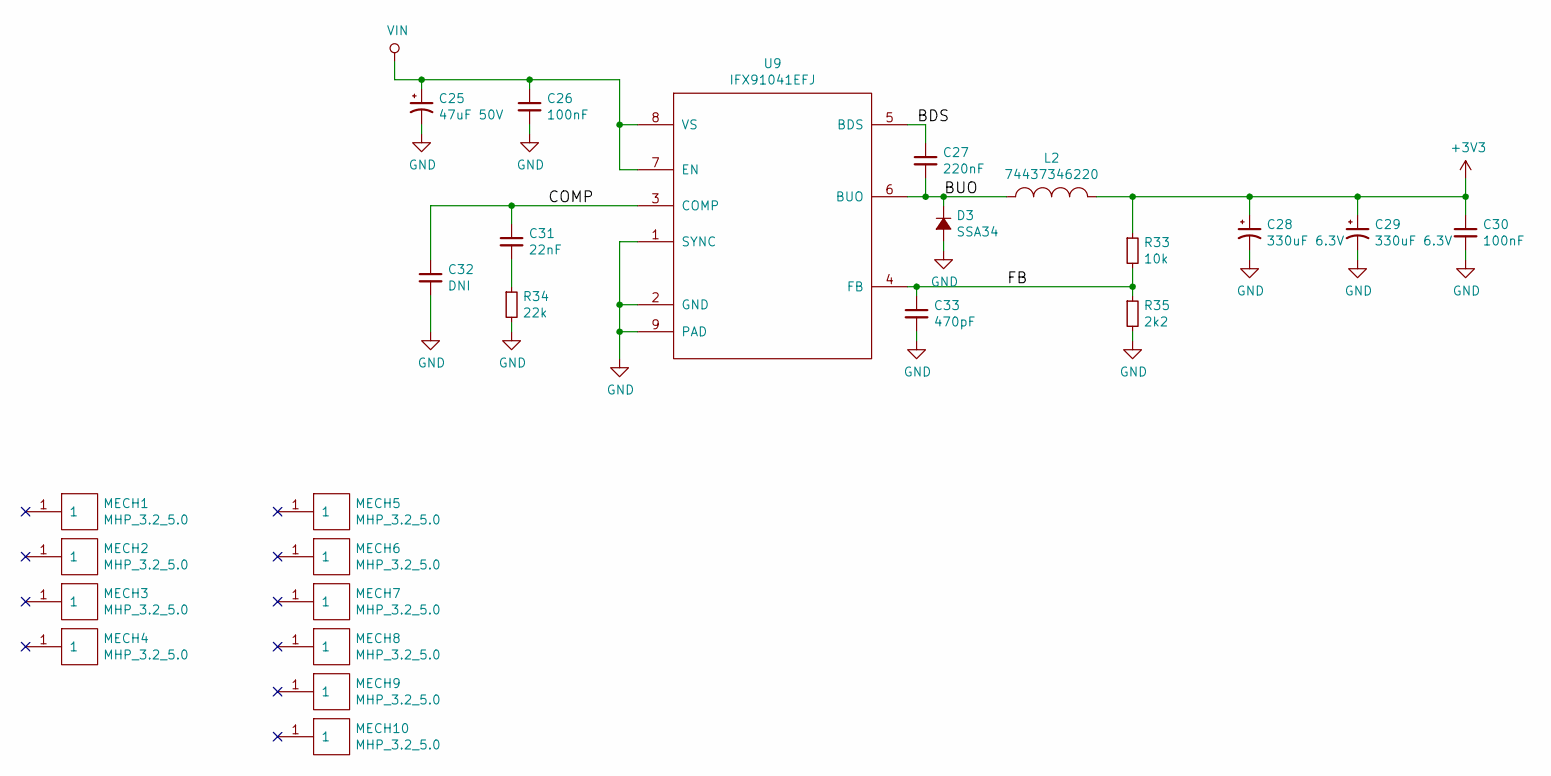
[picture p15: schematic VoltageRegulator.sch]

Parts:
C25: 47uF 50V; TantalC_SizeD_EIA-7343_Wave
C26, C30: 100nF; C_0603
C27: 220nF; C_0603
C28, C29: 330uF 6.3V; TantalC_SizeD_EIA-7343_Wave
C31: 22nF; C_0603
C32: DNI; C_0603
C33: 470pF; C_0603
D3: SSA34; SMA_Standard
L2: 74437346220; WE-LHMI70xx
MECH1, MECH2, MECH3, MECH4, MECH5, MECH6, MECH7, MECH8, MECH9, MECH10: MHP_3.2_5.0
R33: 10k; R_0603
R34: 22k; R_0603
R35: 2k2; R_0603
U9: IFX91041EFJ; SOIC-8-1EP_3.9x4.9mm_Pitch1.27mm

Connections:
+3V3: C28.1, C29.1, C30.1, L2.2, R33.1; also elsewhere on the board
/VoltageRegulator/BDS: C27.1, U9.5 (BDS)
/VoltageRegulator/BUO: C27.2, D3.1 (K), L2.1, U9.6 (BUO)
/VoltageRegulator/COMP: C31.1, C32.1, U9.3 (COMP)
/VoltageRegulator/FB: C33.1, R33.2, R35.1, U9.4 (FB)
GND: C25.2, C26.2, C28.2, C29.2, C30.2, C32.2, C33.2, D3.2 (A), R34.2, R35.2, U9.1 (SYNC), U9.2 (GND), U9.9 (PAD); also elsewhere on the board
unnamed: C31.2, R34.1
VIN: C25.1, C26.1, U9.7 (EN), U9.8 (VS); also elsewhere on the board

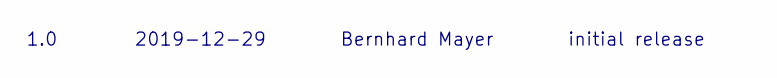
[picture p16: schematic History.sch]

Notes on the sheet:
1.0
2019-12-29
Bernhard Mayer
initial release

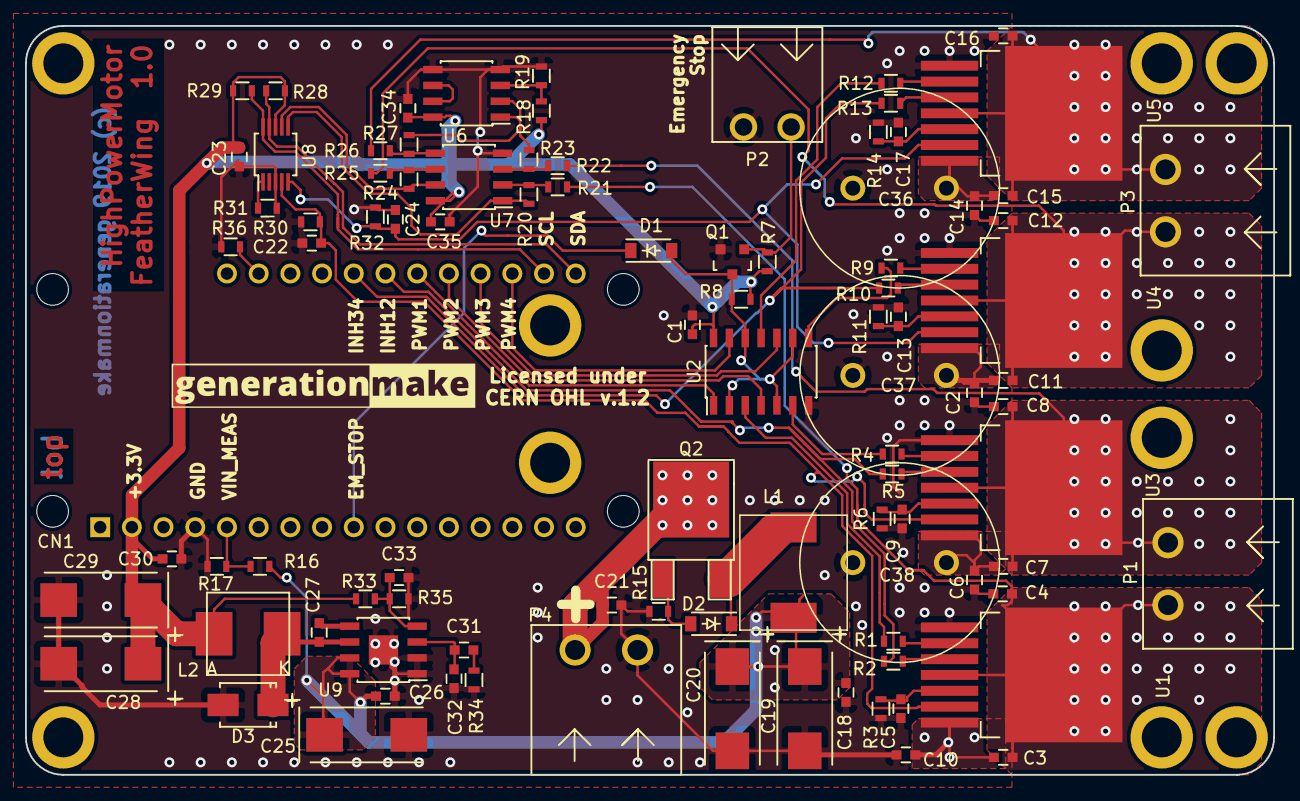
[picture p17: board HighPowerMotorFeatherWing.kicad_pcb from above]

Board: 2 copper layers, 100.0 x 60.0 mm, 105 parts (0 on the bottom side), 56 nets.

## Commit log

2019-12-29 added kicad source
    [HighPowerMotorFeatherWing.kicad_pcb, HighPowerMotorFeatherWing.sch, HighPowerMotorFeatherWing.xml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]
2019-12-29 added values in schematic, generated pdf schematic
    [HighPowerMotorFeatherWing.sch, History.sch, Measurement.sch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]
2019-12-29 added manufacturing pdfs
    [HighPowerMotorFeatherWing.kicad_pcb]
2020-01-01 added mounting instructions
    [HighPowerMotorFeatherWing.kicad_pcb]
2020-01-29 added 3D model for Adafruit Feather connector
    [HighPowerMotorFeatherWing.kicad_pcb]
2020-04-16 changed mounting holes to parts and generated step file
    [HighPowerMotorFeatherWing.kicad_pcb, VoltageRegulator.sch]

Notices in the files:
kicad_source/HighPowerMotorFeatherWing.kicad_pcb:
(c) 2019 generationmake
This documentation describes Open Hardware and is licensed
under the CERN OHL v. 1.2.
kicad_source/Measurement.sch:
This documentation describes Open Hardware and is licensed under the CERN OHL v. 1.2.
